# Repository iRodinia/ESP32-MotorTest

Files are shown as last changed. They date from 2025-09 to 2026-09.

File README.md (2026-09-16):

# ESP32-MotorTest

A Repository for BLDC Test and Data Collection with ESP32 Controller

## Flash BL-32 ESC Firmware (with Arduino Nano)

0. Prepare a Arduino Nano board to serve as the connection interface between PC and ESC:

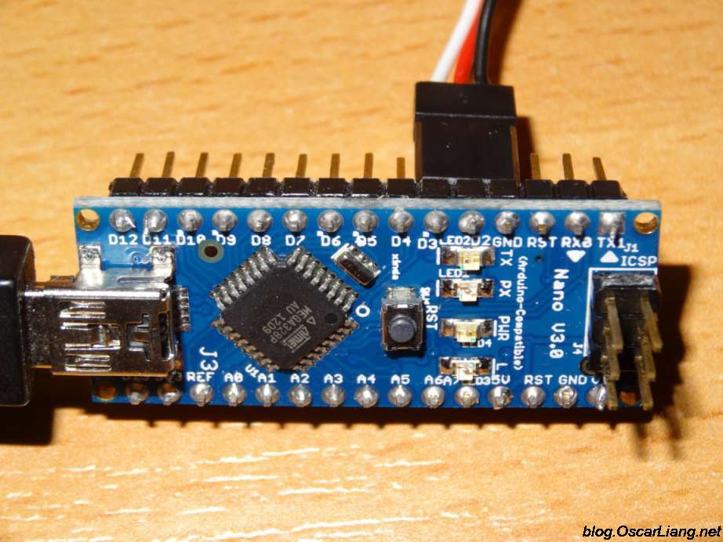
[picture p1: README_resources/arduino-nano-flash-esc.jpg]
arduino-nano-flash-esc Picture of the Arduino Nano


  Pay attention to the port definitions.

1. Connect the Arduino board to the computer with the USB cable, then open the "BLHeliSuit32Test" program.

  You can find a copy of the program in this repository, under the "Tools" folder.

2. Program the Arduino to make the interface:

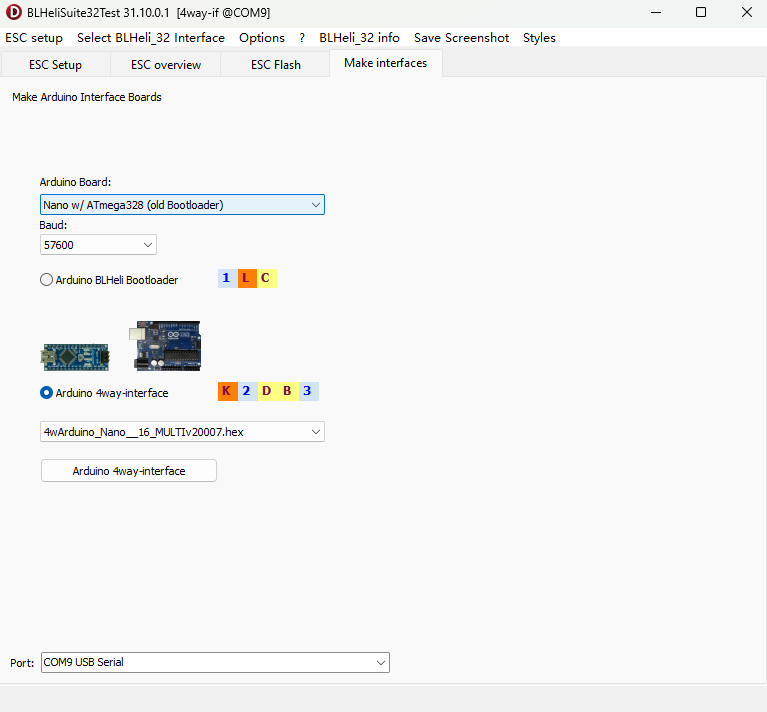
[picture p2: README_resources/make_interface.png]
make_interface Picture of the Make interface session


  Select "Nano w/ATmega328(old bootloader)", then make the 4way-interface. Make sure you have selected the right COM Port at the bottom of this page.

3. Connect the ESC with Arduino:

  As shown in the first figure, connect the signal input of the ESC to Arduino's "D3" port, and the "GND" to any of the "GND" port on the arduino.

  If your Arduino's port configuration is correct and ESC's input port is a 3-pin wire, you can directly plug the ESC to Arduino's "D3-D2-GND" ports without re-wiring.

4. Select the interface in the "BLHeliSuit32Test" program:

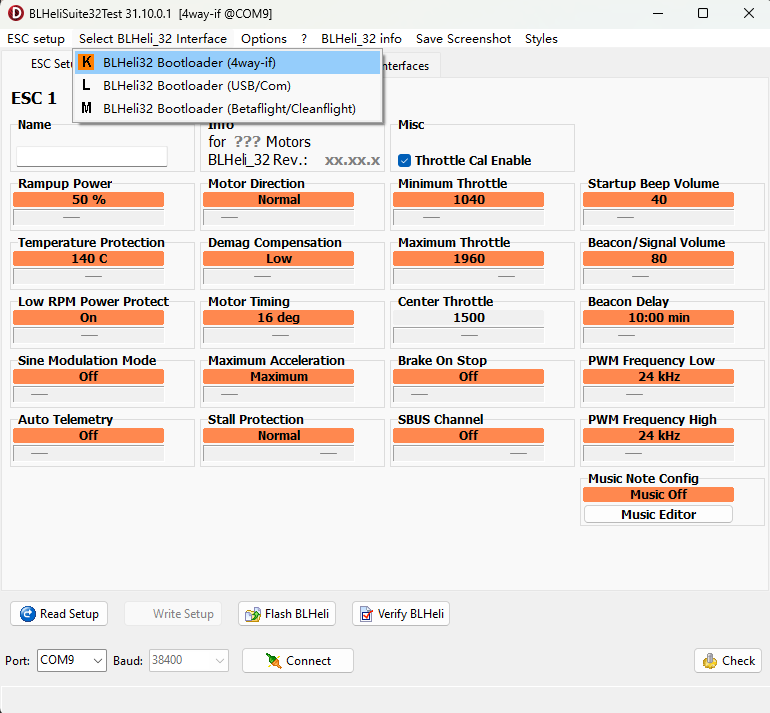
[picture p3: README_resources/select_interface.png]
select_interface Picture of the interface selection


  Choose the interface as "4way-if", then click "Connect". Make sure you have selected the correct COM Port.

5. Read the settings and Adjust:

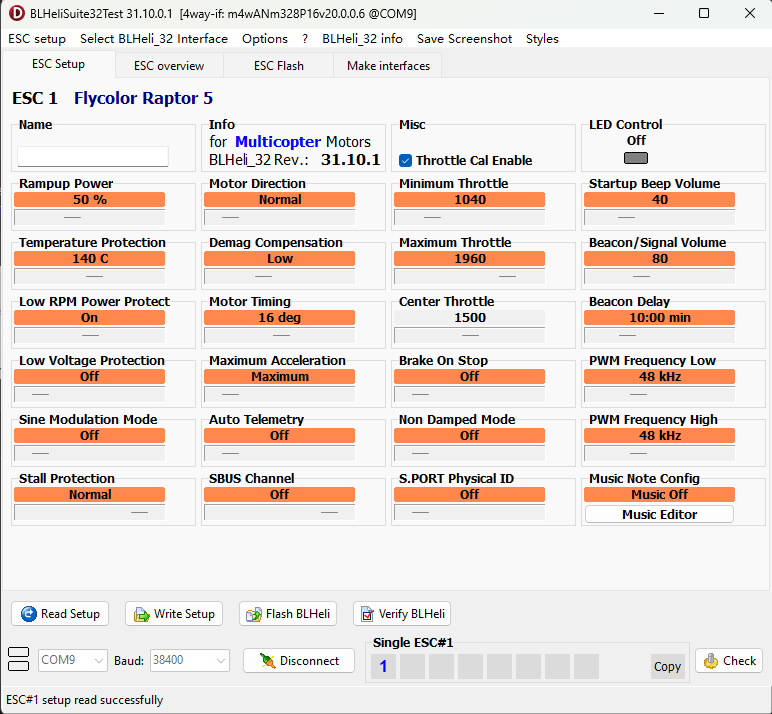
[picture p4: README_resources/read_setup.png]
read_setup Picture of the ESC setup


  Click "Read Setup" and wait for the configurations to be loaded. Then you can make adjustments and click "Write Setup" to refresh the ESC. The descriptions of these setups can be found at "BLHeli_32_Info->manual.pdf".

  **Important**: If you want to collect the voltage, current, temperature or rotation speed from the ESC, make sure to turn "Auto Telemetry" to "On"! (Then the ESC will send back the data once every 32ms) The data is sent through the "Tx" port of the ESC. (See the next subsection for more details)

  If multiple ESCs are used, all the "Tx"s can be connected together to one "Rx" port on the Autopilot or the Microcontroller.

## BLHeli32 ESC Telemetry Protocol Selection

  If you want the ESC to send its sensor data back to your receiver or your MCU, there are **2** ways to do that. Each method requires the **Auto Telemetry** to be switched on. 
  
  First, you connect the "Tx" port of the ESC to the S.Port of your receiver, you must **turn on the "S.Port Physical ID" in the ESC settings**. Then the data will be sent based on the S.Port protocol. 
  
  Second, you connect the "Tx" of ESC to your MCU only, expecting a regular data flow. Then you must **turn off the "S.Port Physical ID"** and read the data following the KISS protocol.

  - For S.Port protocol, please refer to [this link](https://deepwiki.com/marhar/FrSkySportTelemetry/2.2-frame-structure-and-protocol-constants). The S.Port protocol has a baudrate of **57600** and **inverted** signal. The data will only be sent when your receiver (the master device on the wire) send a pooling request first.

  - For KISS protocol, please refer to [this file](Tools/KISS_telemetry_protocol.pdf). The KISS data has a baudrate of **115200** and **normal** signal. The data are sent on a regular time basis even if no device is listening.

## ESP32 Settings

Overview of the ESP32-Wroom-DA module:

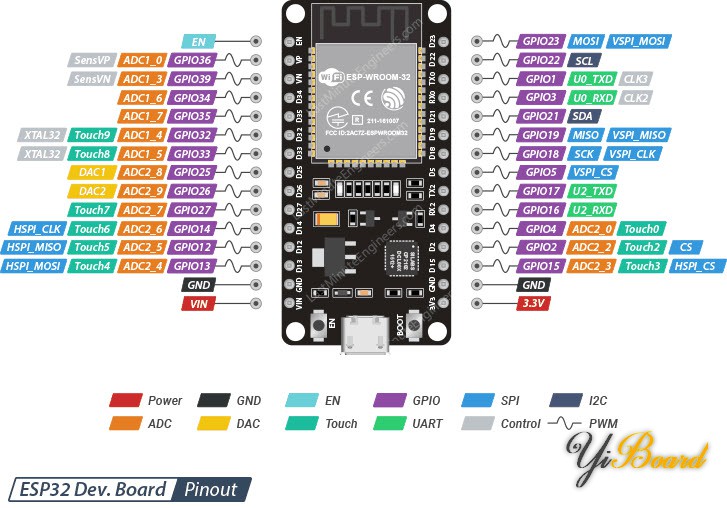
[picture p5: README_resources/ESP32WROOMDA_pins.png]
ESP32WROOMDA_pins Picture of the ESP32 Pins assignments


  The pins assignment here is not always necessary (or correct), because ESP32 allows the user to automatically assign most of its pins for different usage. But the number of Hardware I2C / UART / SPI is fixed.

- Devices Connection (Sensor)

  1. **ADS1115 ADC**: SCL-22, SDA-21, use port A0 to measure power module voltage reading, A1 to measure current reading (in unipolar mode), A2-A3 to measure force (in bipolar mode), A2+/A3-
  2. **ESC Telemetry**: Tx(of ESC)-26, set as the Serial1 Rx pin of MCU
  3. **X8R Receiver SBUS/UART**: Tx(of SBUS/UART board)-27, set as the Serial2 Rx pin of MCU
  4. **MT6701 Magnetic Encoder**: (Remember to enable the SPI output of the module first) CSN-5, CLK(SCK)-18, DO(MISO)-19
  - Warning: GPIO14 and GPIO25 are also occupied due to the usage of Serial1 and Serial2
  - Upload Project: ESP32_MotorTest_Sensors

- Devices Connection (Bridge)

  Just connetc to your PC via usb. (Maybe add an OLED display in the future)
  - Upload Project: ESP32_MotorTest_Sensors_Receiver

- Arduino Libraries Needed
  
  1. **Adafruit ADS1X15** bu adafruit;
  2. **U8g2** by oliver;
  - Remember to install all library dependencies.

- Arduino IDE Settings

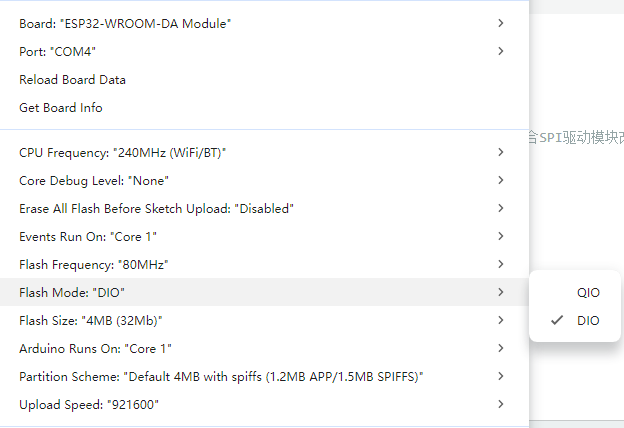
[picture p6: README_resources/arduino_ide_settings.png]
arduino_ide_settings Picture of the Arduino IDE settings
  

## Force Sensor Settings

We use the **AD620** module to amplify the micro-voltage signal from the force sensor itself, then use **ADS1115** to read the voltage signal and transfer to the force readings.

Since the required amplification factor is $\approx440=3.3/7.5\times10^3$, we need to manually change the resistor on AD620 to **$100\Omega$**, which will result in an amplification factor of 495. The maximum voltage output (with 5V input for the force sensor) is 3.712V.

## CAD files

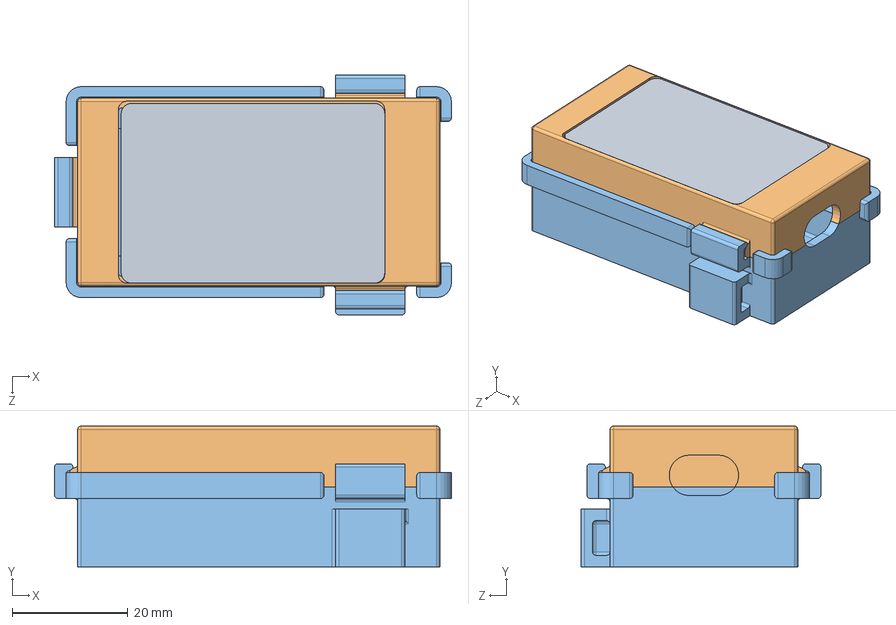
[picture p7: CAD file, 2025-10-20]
Device_Shell/MCU_down_device_asmb.SLDASM
68.5 x 24.3 x 41.4 mm
MCU_down_shell_base
MCU_down_shell_cover
glass-cover

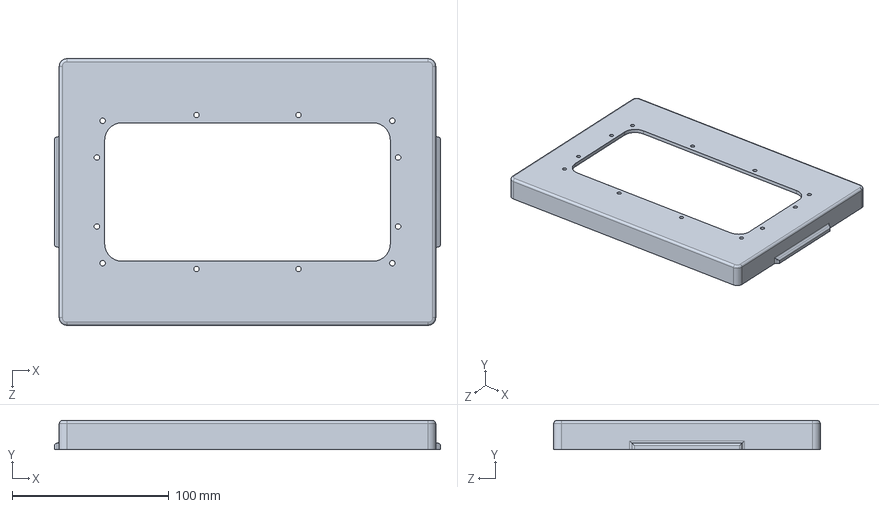
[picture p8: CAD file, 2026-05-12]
Device_Shell/device_box_cover_simple.SLDPRT
246.0 x 18.5 x 170.0 mm

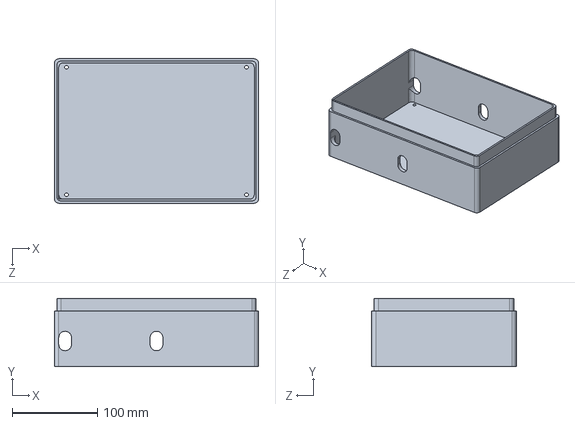
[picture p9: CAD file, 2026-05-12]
Device_Shell/device_box_simple.SLDPRT
240.0 x 80.0 x 170.0 mm

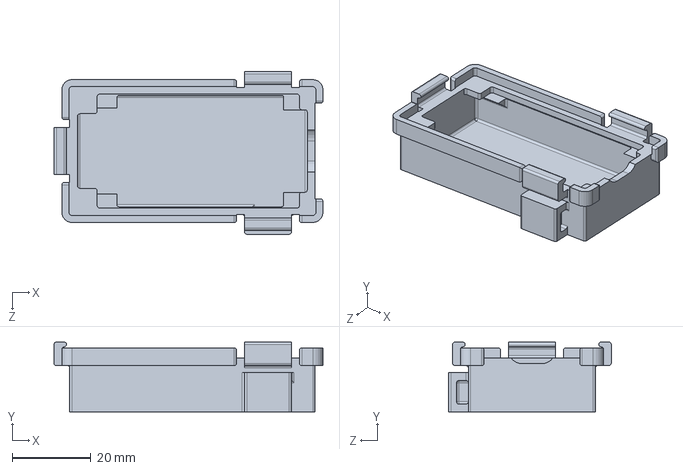
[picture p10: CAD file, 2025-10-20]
Device_Shell/MCU_down_shell_base.SLDPRT
68.5 x 17.8 x 41.4 mm

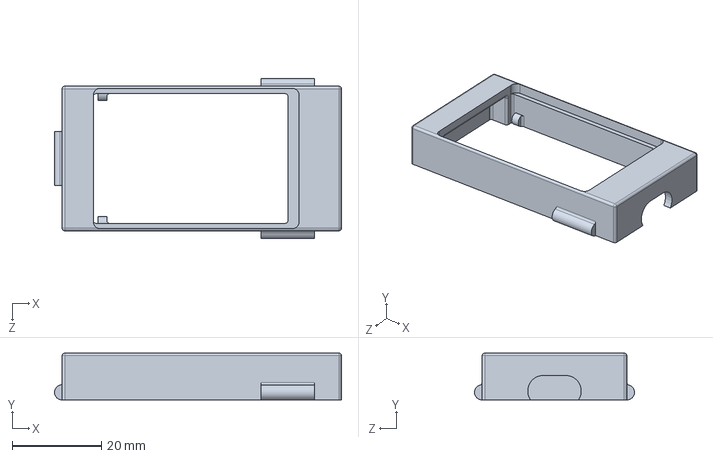
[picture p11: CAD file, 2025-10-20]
Device_Shell/MCU_down_shell_cover.SLDPRT
64.2 x 10.5 x 35.8 mm

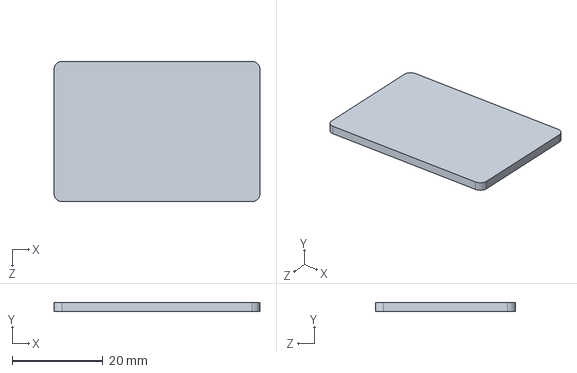
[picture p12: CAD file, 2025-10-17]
Device_Shell/glass-cover.SLDPRT
45.5 x 2.00 x 31.0 mm

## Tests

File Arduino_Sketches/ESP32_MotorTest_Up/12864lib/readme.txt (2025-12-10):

hardware 12864OLED will not work if I2C is also connected with other devices!

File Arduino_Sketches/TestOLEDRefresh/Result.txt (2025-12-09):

Software I2C: loop time 514ms
Hardware I2C: loop time 35ms under fast I2C mode (Wire.setClock(400000))

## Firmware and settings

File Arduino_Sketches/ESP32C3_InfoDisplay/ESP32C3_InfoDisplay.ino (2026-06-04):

// ESP32-C3 — 两块 SSD1306 128x64 OLED + UART1 数据显示
//
// 接线：
//   SCL  → GPIO0       SDA  → GPIO1
//   RX1  → GPIO20      TX1  → GPIO21
//   LED  → GPIO8       BUTTON → GPIO10（另端接 GND，按下低电平）
//   屏幕 INPUT  I2C 地址: 0x7A
//   屏幕 OUTPUT I2C 地址: 0x78

#include <Arduino.h>
#include <Wire.h>
#include "12864_display.h"
#include "Serial_manager.h"

// ── 引脚定义 ──────────────────────────────────────────────────────────────────
#define PIN_LED     8
#define PIN_BUTTON  10
#define PIN_SCL     0
#define PIN_SDA     1

// ── 屏幕实例（地址已按实物对应）─────────────────────────────────────────────
SingleScreen screenA(PIN_SCL, PIN_SDA, 0x7A);   // INPUT  面板
SingleScreen screenB(PIN_SCL, PIN_SDA, 0x78);   // OUTPUT 面板

// ── 运行状态 ──────────────────────────────────────────────────────────────────
int  current_channel = 0;   // 当前显示的通道（0 ~ MAX_CHANNEL_NUM-1）
bool led_state       = false;

// ── 按钮消抖 ──────────────────────────────────────────────────────────────────
namespace Btn {
  bool     lastRaw      = HIGH;
  bool     lastStable   = HIGH;
  uint32_t lastChangeMs = 0;
  const uint32_t DEBOUNCE_MS = 30;

  // 返回 true 表示检测到一次上升沿（按钮松开）
  bool risingEdge() {
    bool raw = digitalRead(PIN_BUTTON);
    uint32_t now = millis();

    if (raw != lastRaw) {
      lastRaw      = raw;
      lastChangeMs = now;
    }

    if ((now - lastChangeMs) >= DEBOUNCE_MS && raw != lastStable) {
      lastStable = raw;
      if (raw == HIGH) return true;   // LOW→HIGH 上升沿
    }
    return false;
  }
}

// ═════════════════════════════════════════════════════════════════════════════
void setup() {
  pinMode(PIN_LED,    OUTPUT);
  pinMode(PIN_BUTTON, INPUT_PULLUP);   // 按下接 GND → 低电平
  digitalWrite(PIN_LED, LOW);

  initAllSerials();
  Wire.begin(PIN_SDA, PIN_SCL);

  screenA.setChannel(current_channel);
  screenA.setHeadLine("INPUT");
  screenA.setLineLabels("Curr:", "Volt:", "CMD :", "Rsrv:");
  screenA.init();

  screenB.setChannel(current_channel);
  screenB.setHeadLine("OUTPUT");
  screenB.setLineLabels("TDeg:", "Forc:", "RPM :", "Rsrv:");
  screenB.init();

}

// ═════════════════════════════════════════════════════════════════════════════
void loop() {
  static float prev_time = 0.0;
  serial1CmdEvent();

  bool data_changed = false;
  if (channel_data[current_channel].time != prev_time) {
    prev_time = channel_data[current_channel].time;
    data_changed = true;
  }

  if (Btn::risingEdge()) {
    current_channel = (current_channel + 1) % MAX_CHANNEL_NUM;
    screenA.setChannel(current_channel);
    screenA.clear();
    screenB.setChannel(current_channel);
    screenB.clear();
    prev_time = 0.0;
  }

  Sensor_Data& d = channel_data[current_channel];
  screenA.updateData(d.esc_current, d.esc_voltage, d.esc_command, 0.0);
  screenB.updateData(d.esc_temperature, d.motor_force, d.motor_rpm, 0.0);
  screenA.refresh();
  screenB.refresh();

  if (data_changed) {
    led_state = !led_state;
    digitalWrite(PIN_LED, led_state ? HIGH : LOW);

    Serial.printf(
      "CH%d | t=%.2fs | V=%.2fV | I=%.2fA | CMD=%.1f%% | T=%.1fdegC | RPM=%.0f | F=%.2fN\n",
      d.channel,
      d.time,
      d.esc_voltage,
      d.esc_current,
      d.esc_command,
      d.esc_temperature,
      d.motor_rpm,
      d.motor_force
    );
  }
}

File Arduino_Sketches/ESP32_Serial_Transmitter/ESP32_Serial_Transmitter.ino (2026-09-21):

// ESP32 Serial Bridge Node
// From Serial 1 to Serial 0

#include <Arduino.h>
#include <Wire.h>
#include "12864_display.h"
#include "Serial_manager.h"

#define SERIAL1_RX 26
#define SERIAL1_TX 25
#define SERIAL1_BAUDRATE 9600

#define SCREEN_SCL_PIN 21
#define SCREEN_SDA_PIN 22  // note: this is not my regular setting

#define PIN_LED 2

bool led_state = false;
bool data_changed = false;
float prev_time = 0.0;
SingleScreen myScreen(SCREEN_SCL_PIN, SCREEN_SDA_PIN);
TaskHandle_t SerialTaskHandle;

void SerialTask(void *pvParameters) {
  for (;;) {
    serial0CmdEvent();
    serial1CmdEvent();

    if (myEscData.lcaT != prev_time) {
      prev_time = myEscData.lcaT;
      data_changed = true;
    }

    vTaskDelay(pdMS_TO_TICKS(2)); 
  }
}

void setup() {
  Serial.begin(115200);
  delay(50);
  Serial1.begin(SERIAL1_BAUDRATE, SERIAL_8N1, SERIAL1_RX, SERIAL1_TX);
  delay(50);
  while (!Serial || !Serial1){
    delay(10);
  }
  
  Wire.setPins(SCREEN_SDA_PIN, SCREEN_SCL_PIN);
  delay(50);
  Wire.begin();
  delay(50);
  Wire.setClock(400000);
  delay(50);

  myScreen.setChannel(0);
  myScreen.setHeadLine("Motor Control");
  myScreen.setLineLabels("Volt:", "CMD :", "RPM :", "Forc:");
  myScreen.init();

  xTaskCreatePinnedToCore(
    SerialTask,
    "SerialTask",
    4096,
    NULL,
    1,
    &SerialTaskHandle,
    0
  );

  pinMode(PIN_LED, OUTPUT);
  digitalWrite(PIN_LED, LOW);
}


void loop() {

  if (data_changed) {
    led_state = !led_state;
    digitalWrite(PIN_LED, led_state ? HIGH : LOW);
    Serial.printf(
      "t=%.2fs | V=%.2fV | CMD=%d | RPM=%.1f | F=%.2fN\n",
      myEscData.lcaT,
      myEscData.lastVol,
      myEscData.lastCmd,
      myEscData.lastRpm,
      myEscData.lastThr
    );

    data_changed = false;
  }

  myScreen.updateData(myEscData.lastVol, myEscData.lastCmd, myEscData.lastRpm, myEscData.lastThr);
  myScreen.refresh();

  delay(5);
}

void parseSerial0Cmd(String command) {
    int target_speed = command.toInt();
    Serial1.printf("%d\n", target_speed);
}

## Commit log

2025-10-20 display fix
    [MCU_down_device_asmb.SLDASM, MCU_down_shell_base.SLDPRT, MCU_down_shell_cover.SLDPRT]
2025-10-29 minor serial bug fix
    [ESP32_MotorTest_Down.ino, ESP32_MotorTest_Up.ino]
2025-12-09 add OLED I2C test
2025-12-09 add I2C OLED
